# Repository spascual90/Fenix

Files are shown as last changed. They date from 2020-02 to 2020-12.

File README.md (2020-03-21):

# Fenix Autopilot
Fenix Autopilot is an open-source DIY tiller pilot for small boats based on Arduino.

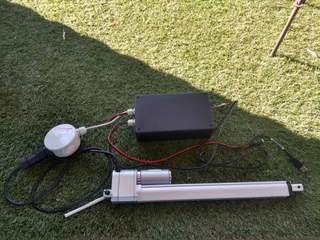
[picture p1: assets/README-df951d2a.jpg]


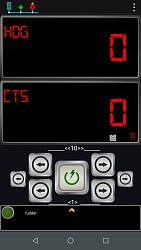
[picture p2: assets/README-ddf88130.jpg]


## Released versions
- V0.1 Initial version

## User Guide
https://spascual90.gitbook.io/fenix-autopilot/

## How to contribute?
Fenix Autopilot is an Open-source project. Source code can be found in Github,
https://github.com/spascual90/Fenix

Fenix Autopilot is developed in the frame of Fenix Project.
The goals of Fenix project are,
- to develop and test a prototype of open-source DIY navigation system for mini-cruisers.  
- to gather individual efforts to a joint solution.
- get users to adopt the system into their own boats with minimum technical knowledge.
All information in Fenix Project can be found here,
https://emacua.fandom.com/wiki/EMacua_Wiki

## How to start with Fenix Autopilot?
First of all integrate your hardware.
If you are a user, upload the SW to Arduino, the App to mobile and configure your autopilot.

If you are a developer, additionally you will have to setup a development environment.
## HW integration
You can find in SCHEMATICS folder,
- Build of materials: the basic shop list to build Fenix autopilot
- Fritzing file
- Guide on how to integrate the components
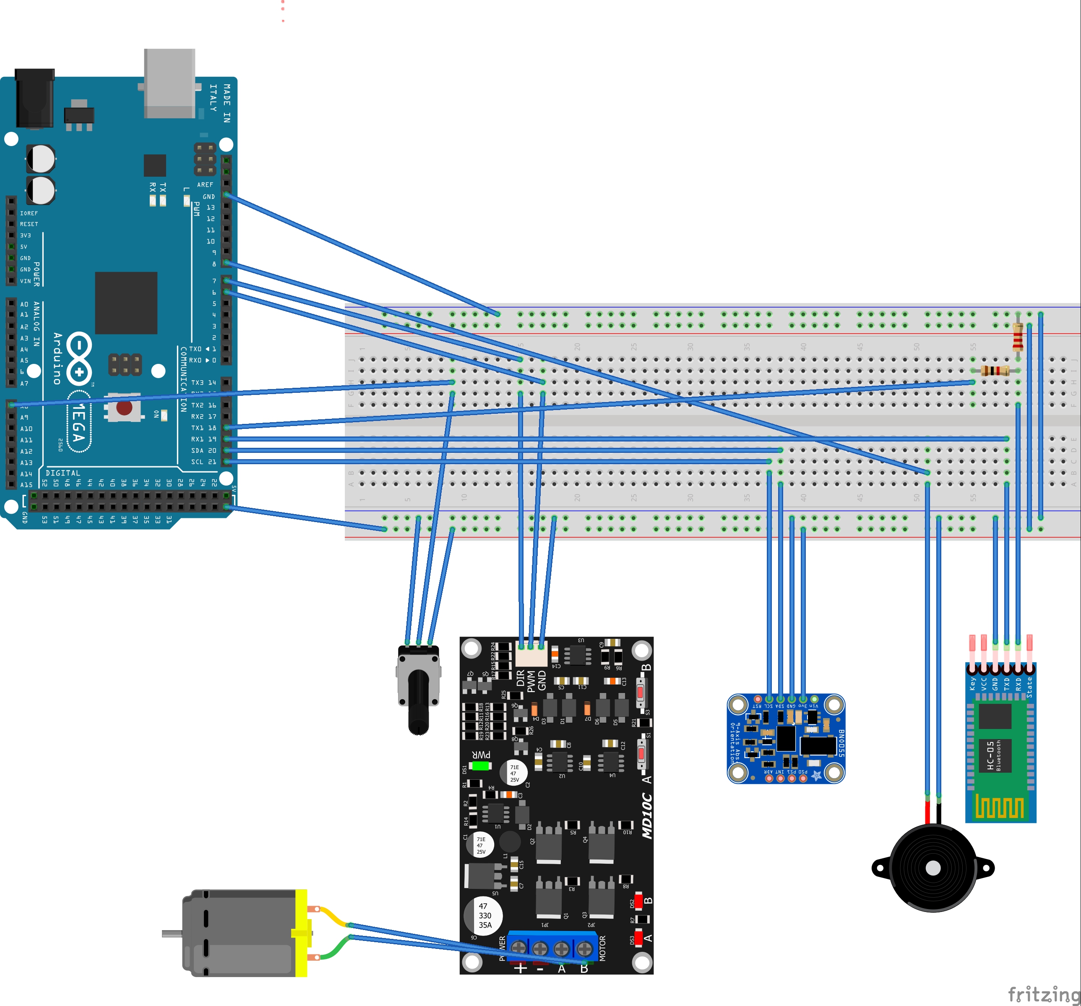
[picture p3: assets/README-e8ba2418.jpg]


## Users: How to start?
### Uploading SW to Arduino
You can find in HEX folder,
- HEX Arduino file
- Xloader, an application to upload HEX to Arduino

### Installing Virtuino App
You can find in repository Virtuino-for-Fenix all elements required
- Enter into Play Store and install Virtuino Viewer
- Copy project file to the Virtuino folder in your mobile
- Configure Bluetooth

### Autopilot configuration
- Connect your laptop to Fenix autopilot USB.
- Open Arduino IDE or putty.exe available in Serial IF folder
- In putty select the Arduino settings
- Open a new terminal
- Follow autopilot information to configure your IMU and linear actuator
- All implemented messages are described in Serial IF folder. A checksum calculator is included.
- Configure other parameters of the autopilot

## Developers: How to start?
### Installation of development environment
Install Sloeber, the Eclipse Arduino IDE https://eclipse.baeyens.it

Downlad Fenix Project from Github https://github.com/spascual90/Fenix

Compile and upload sketch to Arduino

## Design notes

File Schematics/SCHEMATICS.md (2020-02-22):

# Schematics
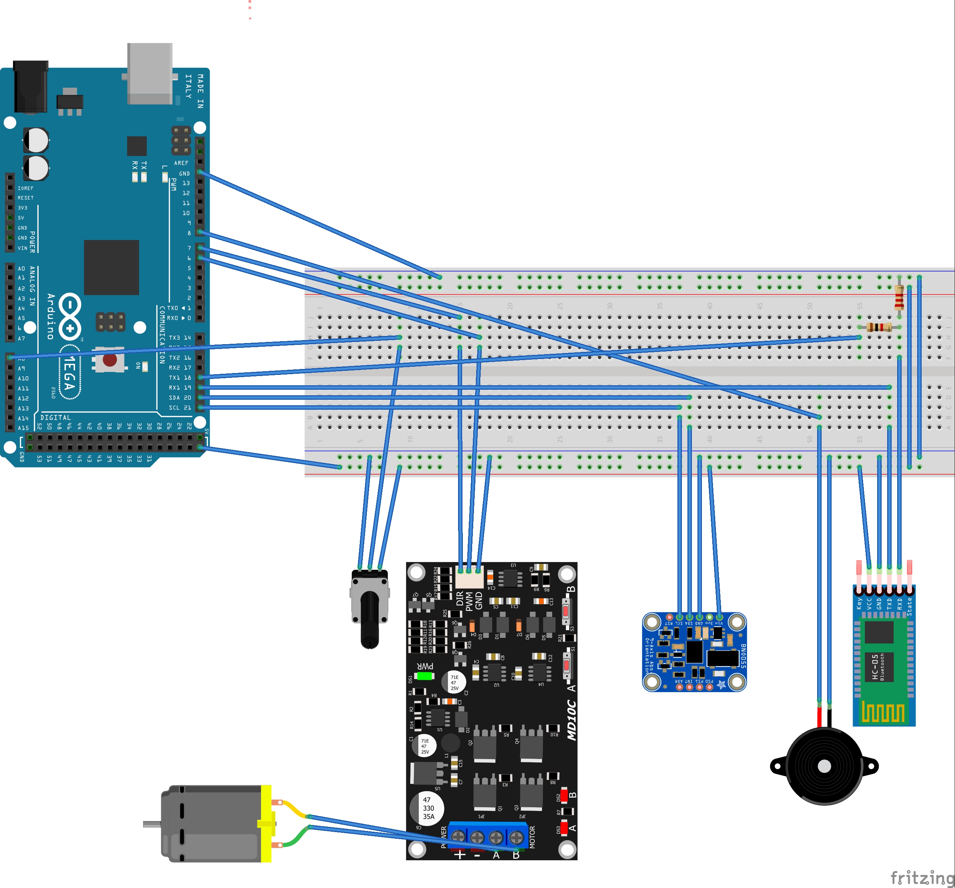
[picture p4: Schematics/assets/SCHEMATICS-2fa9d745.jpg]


## Notes on Schematics & Bill of Materials
- Linear actuator with potenciometer is represented by,
  - M2 - DC Motor
  - R2	Rotary Potentiometer (Small)

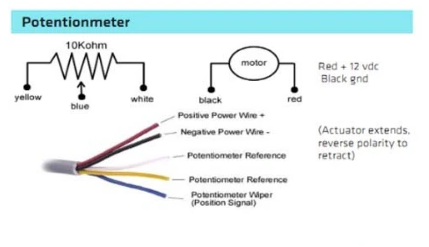
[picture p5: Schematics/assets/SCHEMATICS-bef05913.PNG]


- Alternative DC Motor Driver tested:
  - Cytron MD10C 10A 1 DC motor Driver
  - Cytron 10A 1 DC Motor Driver Arduino Shield

- DC motor driver is powered by a 12V battery not represented.
- Arduino can be powered by 12V battery using a step-down converter to at least 8.5V. Less tension will switch power source to USB leading Arduino to reset if current is too low (USB Laptop OK, Raspberry Pi USB NOK).
- Breaker at the 12V entry should be used for security.

## Notes on IMU BNO055
- I2C shall be connected to GND
- Shortcircuit S0 and S1 negative poles
- Install oscilator into available places

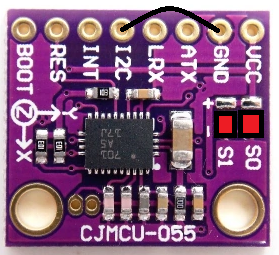
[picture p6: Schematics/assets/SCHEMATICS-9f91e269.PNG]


## Notes on HC-05 BT
- BT shall be configured to 38400 Bauds. Use BT_AT_Mode sketch

# Prototype assembly






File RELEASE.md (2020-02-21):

# RELEASE
## Version: 0.1
## System requirements
| Req.ID# | Description | Criticity | Implemented |
| --- | --- | --- | --- |
| SR-1 | Minimize cost of adquisition. Based on COTS components and integrate Open-source projects as possible | High | Yes |
| SR-2 | Ease integration with other systems or components by using industry standards. | High | Yes |
| SR-3 | Ease system adoption from developers and users with appropriate documentation, minimizing requirements for technical knowledge on electronics, physics or SW. | High | No |
| SR-4 | Modular approach priorizing escalability of components to implement requirements in later stages. Use of object oriented code. | High | Yes |
| SR-5 | Provide test means in order to ease testing and recording of results | High | Partial |

## Autopilot requirements implemented
| Req.ID# | Status | Description | Priority |
| --- | --- | --- | --- |
| AP-3 | Closed | Minimize power consumption | High |
| AP-4 | Closed | Internal compass tilt compensated | High |
| AP-6 | Closed | Calibration procedure for internal compass before installation supported by Autopilot without additional OEM SW. | High |
| AP-7 | Closed | Compensation of permanent deviation of installed compass with reference to the bow. | High |
| AP-18 | Closed | USB electrical interface. | High |
| AP-19 | Closed | Alternative NMEA 0183 version 2.x or | High | er electrical interface (RS422). | Nice to have
| AP-20 | Closed | NMEA 0183 data protocol at least versions 2.x to 4.x (4800 baud, w/o parity, 8 bits,1 bit stop) | High
| AP-22 | Closed | Reception of minimum autopilot information required for Nav mode | High
| AP-24 | Closed | Transmision of internal compass magnetic course. | High
| AP-25 | Closed | Transmision of tiller position. | Low
| AP-27 | Closed | Stand-by mode provides user capability to command linear actuator changes in and out by short and long leaps. | High
| AP-28 | Closed | Compass mode. Autopilot will follow the current course. | High
| AP-31 | Closed | Nav mode. AP will bear to a Waypoint by following the required course received from an external source. | High
| AP-34 | Closed | User definable central position of tiller | High
| AP-35 | Closed | Adjust AP bearing during Autopilot mode by 1º or 10º | High
| AP-39 | Closed | Ensure safety of the operations by requiring user confirmation before proceed and/or sound warning (i.e. error, start, stop, tack, decission/ action of user required...). | High
| AP-40 | Closed | Minimum recomended motor controller performance: Bidirectional single-brushed. Support motor voltage to 16V. Support continous current: 10 A | High
| AP-41 | Closed | Voltage threshold: 10-16V | High

# Autopilot requirements not implemented

| Req.ID# | Status | Description | Priority |
| --- | --- | --- | --- |
| AP-2 | Closed | Protection by design of mechanical and electronic parts from blockage, intense use, short-cirtuit and humidity. Parts exposed to weather conditions shall have IPX4 equivalent protection. | High |
| AP-5 | Closed | Capability to use as alternative an external compass  | Nice to have |  
| AP-9 | Closed | Mounting at starboard or portboard | High |
| AP-10 | Open | Autotrim of tiller to keep current heading when lateral forces (wind, tide, non-centered engine) require permanent correction of tiller to follow the current way-route. Maximum 1 minute for autotrimming. | To be cheked | | | | |
| AP-11 | Closed | Predefined pilot gain configurations for different speeds and boats. | High  |
| AP-12 | Closed | Autogain for different SOW (speed over water).  | Low |
| AP-13 | Closed | If SOW is not available, user configurable speed shall be used. | AP.-14  | Closed | User configurable gain for testing purposes. | High |
| AP-15 | Closed | Capability to record required parameters to analyze AP performance for different external conditions for testing purposes. | High |
| AP-16 | Closed | Different deadband configurations for bad weather conditions: predefined, user defined, desactivated. | High |
AP-17 | Closed | Automatic deadband configuration  | Nice to have |  
 AP-21 | Closed | Reception of magnetic/real course from external compass | Nice to have |
AP-23 | Closed | Reception of SOW information from nautical slide. In Km or nautical miles. | Low |
  | AP-26 | Closed | Reception of real and apparent wind information. | High |
  | AP-29 | Closed | Wing mode. AP will maintain current Apparent Wind Angle. | Medium |
  | AP-30 | Closed | Wind mode is only possible when wind information is available from an external source. | Medium |
  | AP-32 | Closed | Nav mode. If not available from external source, the required course will be BTW. | Nice to have |
  | AP-33 | Open | Central position of tiller is by default considered the position where Autopilot is set to Compass mode. | Low |
  | AP-36 | Closed | Tack starboard/ portboard in Compass mode. AP will turn by 100º the current heading in the direction selected by the user. | High
| AP-37 | Closed | Tack in Wind mode. AP will turn to head the same Real Wind Angle but on the oposite band. Turn direction will be selected by AP as the shortest path to reach the target heading. | High |
 | AP-38 | Closed | Tack in Nav mode is not possible. | High |
  | AP-42 | Open | Maximum thrust torque (at the end of the tiller): 250N. Minimum angular speed (tiller): 0 Kg: TBD º/sec 35 mm/seg 20 Kg: TBD º/sec 30 mm/seg 40 Kg: TBD º/sec 20 mm/seg | High |

## Requirements partially implemented
| Req.ID# | Status | Description | Priority |
| --- | --- | --- | --- |
| AP-8  | Closed | Procedure to define installation parameters supported by Autopilot without additional SW. | High |

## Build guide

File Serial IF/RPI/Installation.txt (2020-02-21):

Install and Run Putty on your Raspberry Pi
Putty is a very useful application that can be used to connect to serial ports and Secure Shell(SSH) to Raspberry Pi’s.

Putty is mostly used on Windows to connect to remote devices but it can also run on a Raspberry Pi.

Steps to installing Putty on a Raspberry Pi:

Open a terminal/shell window on your Raspbery Pi and run the following command:
sudo apt-get install putty -y
After the installation Putty should appear in the menu bar under the ‘Other’ menu.

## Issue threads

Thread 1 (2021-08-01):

conflict between libraries (multiple definitions)

elgui, 2021-08-01:
I'm using the provided versions of external librairies, and the build fails due to "multiple definition" of many sorts.
I have read that it comes from conflicting librairies, using the same interupt pin or timer.

```
Disabling relaxation: it will not work with multiple definitions
make: *** [makefile:93: Fenix.elf] Error 1
multiple definition of `__vector_25'
multiple definition of `__vector_26'
multiple definition of `__vector_36'
multiple definition of `__vector_37'
multiple definition of `__vector_51'
multiple definition of `__vector_52'
multiple definition of `__vector_54'
multiple definition of `__vector_55'
multiple definition of `NeoHWSerial::available()'
multiple definition of `NeoHWSerial::begin(unsigned long, unsigned char)'
multiple definition of `NeoHWSerial::end()'
multiple definition of `NeoHWSerial::flush()'
multiple definition of `NeoHWSerial::peek()'
multiple definition of `NeoHWSerial::read()'
multiple definition of `NeoHWSerial::write(unsigned char)'
multiple definition of `NeoSerial'
multiple definition of `NeoSerial1'
multiple definition of `NeoSerial2'
multiple definition of `NeoSerial3'
```

spascual90, 2021-08-01:
Hello, difficult to analyze as I am on holidays, no access to my test platform... sorry.
I think this is related to wrong configuration of the library path folders.
Are you using Eclipse or the Arsuino IDE?
If you give more info related to this topic I may help for troubleshooting.

Regards
Sergio

elgui, 2021-08-03:
Hello Sergio,
thank you for answering while being in vacations !
Following your  hint, I found the problem : I had duplicate NeoHWSerial files...
I have struggled so much to setup that workspace that it endep-up a bit messy.. But now it works, and as a developer, I'm super happy to further participate in that project !
I keep you posted, enjoy your holidays =)
PS: I am anchored in the South-West of Andalucia (just in case)

Closed 2021-08-03.

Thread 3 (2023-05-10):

BOM

tcurdt, 2023-05-10:
Quick correction of the docs:
A BOM is a "Bill of Material".

Very cool project!

spascual90, 2025-01-05:
Thank you and apollogize for the very late answer. Will check the documentation and fix.
Regards
Sergio

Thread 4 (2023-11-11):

JP2-Kypad

Max194703, 2023-11-11:
Hi, is it possible to add a keypad?

spascual90, 2025-01-05:
Hello,
the short answer is currently no, but can be developed.
I started developing Fenix using a keypad and evolved to a bluetooth connection to the mobile, which provides robust connection and better graphic interface. Keypad code was discontinued and nowadays not supported.
Alternative: I recently checked USB connection from Fenix to a mobile using an OTG cable and Serial USB Terminal. If you want a wired connection, this is a good alternative using NMEA messages for basic functions (RUN/STAND BY, TURN STARBOARD/ PORTBOARD). I will further develop this idea soon in a video.

Regards
Sergio

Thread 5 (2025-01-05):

Use with PyPilot motor controller

mgrouch, 2025-01-05:
I have Pypilot motor controller for hardware. And bunch of esp32 from m5stack. I’d like to see if I can use fénix autopilot MCU to control motor controller from Pypilot.
I didn’t do much of homework on this yet but I’d appreciate any leads.

Thanks

spascual90, 2025-01-05:
Hello,
Fenix has a standard PWM based control interface. If Pypilot uses this standard it will be easy to integrate.

I had a look to the documentation available for the Pypilot motor controller but it requires time to understand... I think Pypilot is a project much more complex than Fenix with a lot of implementation alternatives and configurations.

It would be interesting to other users moving from Pypilot to Fenix to know if they can reuse part of their hardware. Any progress on this will be welcome!

Regards
Sergio

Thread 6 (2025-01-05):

Ordering PCB

mgrouch, 2025-01-05:
Is there a way to ask https://jlcpcb.com/
(as it seems it’s most common)
instead of uploading the schematics again
just to provide some reference number of previous order and repeat it? I think it would simplify the process for manufacturer and end user as well.

Thanks

spascual90, 2025-01-05:
Hello,
I am not aware of it. If you find it, let me know what is the required code and I will check in my last order if I can provide it to you.
However, if you need help to order on jlcpcb.com let me know and I will be glad to support.
Regards
Sergio

Tempest2k8, 2025-01-22:
@mgrouch I have extra boards, as the minimum order was 5. I've ordered the other parts for the shield from Aliexpress and can package them in a kit if you would like one.

Chris

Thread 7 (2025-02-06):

IMU Out of range / ICM20948

PlavB, 2025-02-06:
Hello,

I am having issue calibrating the IMU Sensor from Sparkfun. Using the python software as shown in the recent youtube video.

After calibrating i get the error message "IMU offsets out of range" after it uploades the NMEA Sentence for each of the offsets(Gyro, Acc and mag)

Testing the accuracy after uploading the data to arduino it is working ok with some deviation, but after a reboot it will be way off with the heading accuracy. Often being stuck between a certain posistion range (e.g: 120 - 190).

I have tried to calibrate it a few times at different locations, could this be an issue? And is it possible to remove previous data/calibration attempts?

spascual90, 2025-02-07:
Hello.
Please send me all files generated by python calibrator and will check.

Thank you
Sergio

El vie, 7 feb 2025, 1:25, PlavB ***@***.***> escribió:

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

PlavB, 2025-02-07:
Hello,

See attached file. Thanks.

[Fenix_ICM_20948_Cal-Out of range.zip](https://github.com/user-attachments/files/18704404/Fenix_ICM_20948_Cal-Out.of.range.zip)

spascual90, 2025-02-07:
Hello,
after reviewing your files everything is correct. I used those with my Arduino and it loaded all three NMEA sentences without error message.
You can see attached the output file from the serial comunication with Arduino.

This is the info I got from your files,

*************************
******* GYROSCOPE *******
*************************
G_offset[3] = { -83.13,-118.02,31.29 };

*************************
NMEA Sentence for Fenix Autopilot :
*************************
$PEMC,14,-83.13,-118.02,31.29,0.00000,0.00000,0.00000,0.00000,0.00000,0.00000,0.00000,0.00000,0.00000,G*63

*************************
***** ACCELEROMETER *****
A_B[3] = {-3.39,-255.08,365.69 };

A_Ainv[3][3] = {
{ 0.06021 , 0.0027 , 0.00081 },
{ 0.0027 , 0.06175 , -0.00059 },
{ 0.00081 , -0.00059 , 0.05993 }};
*************************
NMEA Sentence for Fenix Autopilot :
*************************
$PEMC,14,-3.39,-255.08,365.69,0.06021,0.00270,0.00081,0.00270,0.06175,-0.00059,0.00081,-0.00059,0.05993,A*65

*************************
***** MAGNETOMETER *****
*************************
M_B[3] = {124.03,295.09,30.58 };

M_Ainv[3][3] = {
{ 3.11726 , 0.08012 , 0.23037 },
{ 0.08012 , 3.4981 , -0.00322 },
{ 0.23037 , -0.00322 , 2.82628 }};

*************************
NMEA Sentence for Fenix Autopilot :
*************************
$PEMC,14,124.03,295.09,30.58,3.11726,0.08012,0.23037,0.08012,3.49810,-0.00322,0.23037,-0.00322,2.82628,M*5D

According to Arduino code, the error message shall pop up when any of the values exceed the following limits,
G_offset[3] +-1000
A_B[3] +-1000
M_B[3] +-1000
A_Ainv[3][3] +-50
M_Ainv[3][3] +-50

And the NMEA sentences you generated are within the limits. There should not be any error.

Can you copy the serial output with Arduino so I can see the error message in context?
To do so, just select all lines and copy (press Ctrl+C) then paste to a .txt file.

Thanks
Sergio

[Serial_output.txt](https://github.com/user-attachments/files/18710308/Serial_output.txt)

PlavB, 2025-02-07:
Hello,

I can see that it failed to load the install parameters, for your information, i have not changed any settings.

[Copy of serial output.txt](https://github.com/user-attachments/files/18710531/Copy.of.serial.output.txt)

spascual90, 2025-02-07:
Please repeat the process to send 3 nmea sentences and send the serial so I can see the error.
Thank you

Regards
Sergio

PlavB, 2025-02-07:
Hello,

This should be it:

[Serial output nmea.txt](https://github.com/user-attachments/files/18711250/Serial.output.nmea.txt)

spascual90, 2025-02-07:
Try to load in a different order. First M then G and finally A.
Regards
Sergio

El vie, 7 feb 2025, 23:54, PlavB ***@***.***> escribió:

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

PlavB, 2025-02-07:
Same issue, unfortunatly.

Sensor is working ok after sending the offset data, but as soon as it is being rebooted it gets the same error .

PlavB, 2025-02-07:
Hello again,

I might have found the issue. I cleared the EEPROM using the example code "EEPROM_Clear" in the arduino IDE software.

Reinstalled the HEX File and the calibrator data. Now after several reboot it keeps the same offsets and no alarm.

There were probably too many different configurations stored in the EEPROM. During the installation process i also tested with the BNO055 IMU.

Just one question regarding the Serial interface. I am not able to send commands through either Arduino IDE or Putty. It does not respond, is there an easier way to send the commands?

Thank you for your help so far. :-)

spascual90, 2025-02-08:
Good to hear that. I will think about an instruction to reset the eeprom.
For serial communication with Arduino ide, once  Board and Port are selected, you should configure the monitor at 9600 Baud and "No line ending" option.
It works for me.
Regards
Sergio

PlavB, 2025-02-10:
Hello,

I think I was a little quick to confirm that everything was working 100%. Sorry about that.

It seems that when I try to change the settings in the Installation Parameters/PID Parameters, the IMU offset is again going out of range.

I can set up the IMU with the calculated offsets just fine, but when I try to change the parameters, save, and then reboot, the offsets are gone from the Arduino. If I try to do it in reverse; changing the parameters first and then uploading the offsets, the parameters are gone, but the IMU offsets remain.

I can also mention that i am not able to save the Installation Parameters at first with a fresh HEX installation.(Prompted with Failed to restore inst.parameters, loading default")

I have to install the "Simulator" HEX file to save the installation parameters once, then go back to the ICM HEX file, after that i am fully able to change and save the installation parameters. But it seems i am not able to save both installation/PID parameters and the IMU offsets. Could there be anything wrong with my Arduino? It is a fresh unit.

Regards,

Olav H.

spascual90, 2025-02-10:
Thank you to your comments I identified a bug in the code.
Please check new pre-release and give feedback. It should fix the issues you are facing. All IMU, Inst.Parameters are related to overwritting directions in EEPROM.

https://github.com/spascual90/Fenix/releases/tag/v3.4beta2

Regards
Sergio

PlavB, 2025-02-10:
Hello,

I have now tested it, and it has resolved the issue. Tried to change the settings on both installation and pid parameters after setting up the IMU offsets and it worked wonders. Thank you.

I will do a another sea trial tomorrow. 👍

Regards,

Olav H.

spascual90, 2025-02-11:
Good to hear that!
Please make video and picture of your installatuon and share experience!
Regards
Sergio

El lun, 10 feb 2025, 22:54, PlavB ***@***.***> escribió:

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

Closed 2025-02-11.

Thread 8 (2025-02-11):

Installation parameters / Sea trial questions

PlavB, 2025-02-11:
Hello,

Some question/findings during sea trial(Sorry for the repetetive questions, i am not so familiar with fault finding in code),

I am not able to change the average cruise speed in the installation parameters.(System in standby-mode).

I noticed that when choosing a CTS/HDG, example: 120. At standstill the rudder is fixed to the correct heading, but as soon as i accelerate the boat it turns 180 degree and follows that heading, so if i choose 120, when boat start to move, it will follow the HDG of 300 degrees.

Can this be because i can't change the average cruise speed? Or is this about the heading allignment? My boat is capable of moving about 15-16knots maximum. But cruising is more like 5-10 knots.

Just to clarify, Is the Centered tiller posistion setting supposed to be the potentiometer value when tiller is alligned with the hull? For example mine is showing 338 in the actuator calibration menu in the application, should this value be the setting in the installation parameters? Or is it always 0?

Note; I also noticed that i can not change the mounting posistion of the actuator. Not a real problem for me, since mine is mouinted on Starboard side.

Thank you very much for your support.

Olav H.

PlavB, 2025-02-11:
Additional note,

I am not able to change the rudder angle parameter. it is locked to default 511.

spascual90, 2025-02-12:
Hello,
Average Cruise is currently not used by the autopilot. Is there for future improvements.

To start to work you just have to go through calibration of linear actuator.
To check good calibration, on stand by press > button until the actuator is fully extended and then press < until it is fully retracted. Finally press Start and it should go to the center position.

For more information about the 180 turn I would need the serial dump again and/or some videos.

Regards
Sergio

spascual90, 2025-02-12:
> Additional note,
>
> I am not able to change the rudder angle parameter. it is locked to default 511.

Do you mean maximum rudder angle?
511 should be the standard value. Change only if you want to limit the extension of linear actuator.
Regards
Sergio

spascual90, 2025-02-13:
And IMU device shall be placed horizontal with the components on top and away from magnets like buzzer or boat engine.
Regards
Sergio

PlavB, 2025-02-13:
Hello, Sorry for delayed answer. Didnt have the oppertunity to go on a boat trip until today.

Thanks for clearifying the questions.

I think the IMU  is placed away far enough from magnets and engine. Engine is 1 meter approx.

Check the link for video of the problem regarding heading being 180 degree out when in motion. I tried the heading allignment without change.

Serial dump:

[Serial dump.txt](https://github.com/user-attachments/files/18787272/Serial.dump.txt)

Link for video and picture of connection box:

https://1drv.ms/f/c/3776124397745f29/Epm12N7_6bxEgwY9ot4zWtEBdGheQyx0pYUHzCZe9nfNkg?e=9gyMWR

spascual90, 2025-02-13:
Hello,
looking at your PID parameters,
$PEMC,05,1.00,0.05,0.00,100,A*74
I think the problem is that the rudder gain (P value of PID) is 1 which is very low. The rudder is not turning enough to steer the boat to the targeted direction.
Try Proportional gain P=8.00 to start.
$PEMC,06,8.00,0.00,0.00,100,m*57

Here a link on how PID works and what is the behaviour of the autopilot depending on the value of P, I, D parameters.
https://www.bandg.com/blog/autopilots-understanding-performance-functions/

You can follow this guide to calibrate your PID values that fit to your boat's behaviour. Start with P, then I and finally D.

Regards
Sergio

PlavB, 2025-02-13:
Hello,

I will check tomorrow. Thanks.

I was experiencieng a lot of sway with 8. I supose i didn't use the I and D correctly.

Will revert with the results!

spascual90, 2025-02-19:
Hello,
Any progress? Tweaking PID parameters to get good results can be difficult. I have no trusted process defined. Whether to start with I then PD or PD then I...
Regards
Sergio

PlavB, 2025-02-19:
Hello,

I havent had so much time to go out and test since it has been snowing a lot.

I tried with only changing the PD but i get too much side to side movements, i find it to work best with P: 1 and D: 0,5 so far.
I will try changin the I first as well.

Maybe the actuator is too slow or the rudder angle is too big? i will try to adjust this on the next test run.

Just to mention, i still have the issue that it is tracking 180⁰ wrong. Even with P being 8.

I have also noticed that i can only change next CTS by turning the heading weel towords starboars and not portside.

PlavB, 2025-06-06:
Hello,

I haven’t had much time to test due to work.
I’m sure I calibrated the actuator correctly, but I’ll definitely double-check it. Thanks for noticing.

Will revert as soon possible. But i dont think i will get the chance untill august, unfortunatly.

Regards, Olav

spascual90, 2025-06-08:
Maybe you did not save after calibration? Please let me know any progress. Also complete log would help to sort out.
Sergio

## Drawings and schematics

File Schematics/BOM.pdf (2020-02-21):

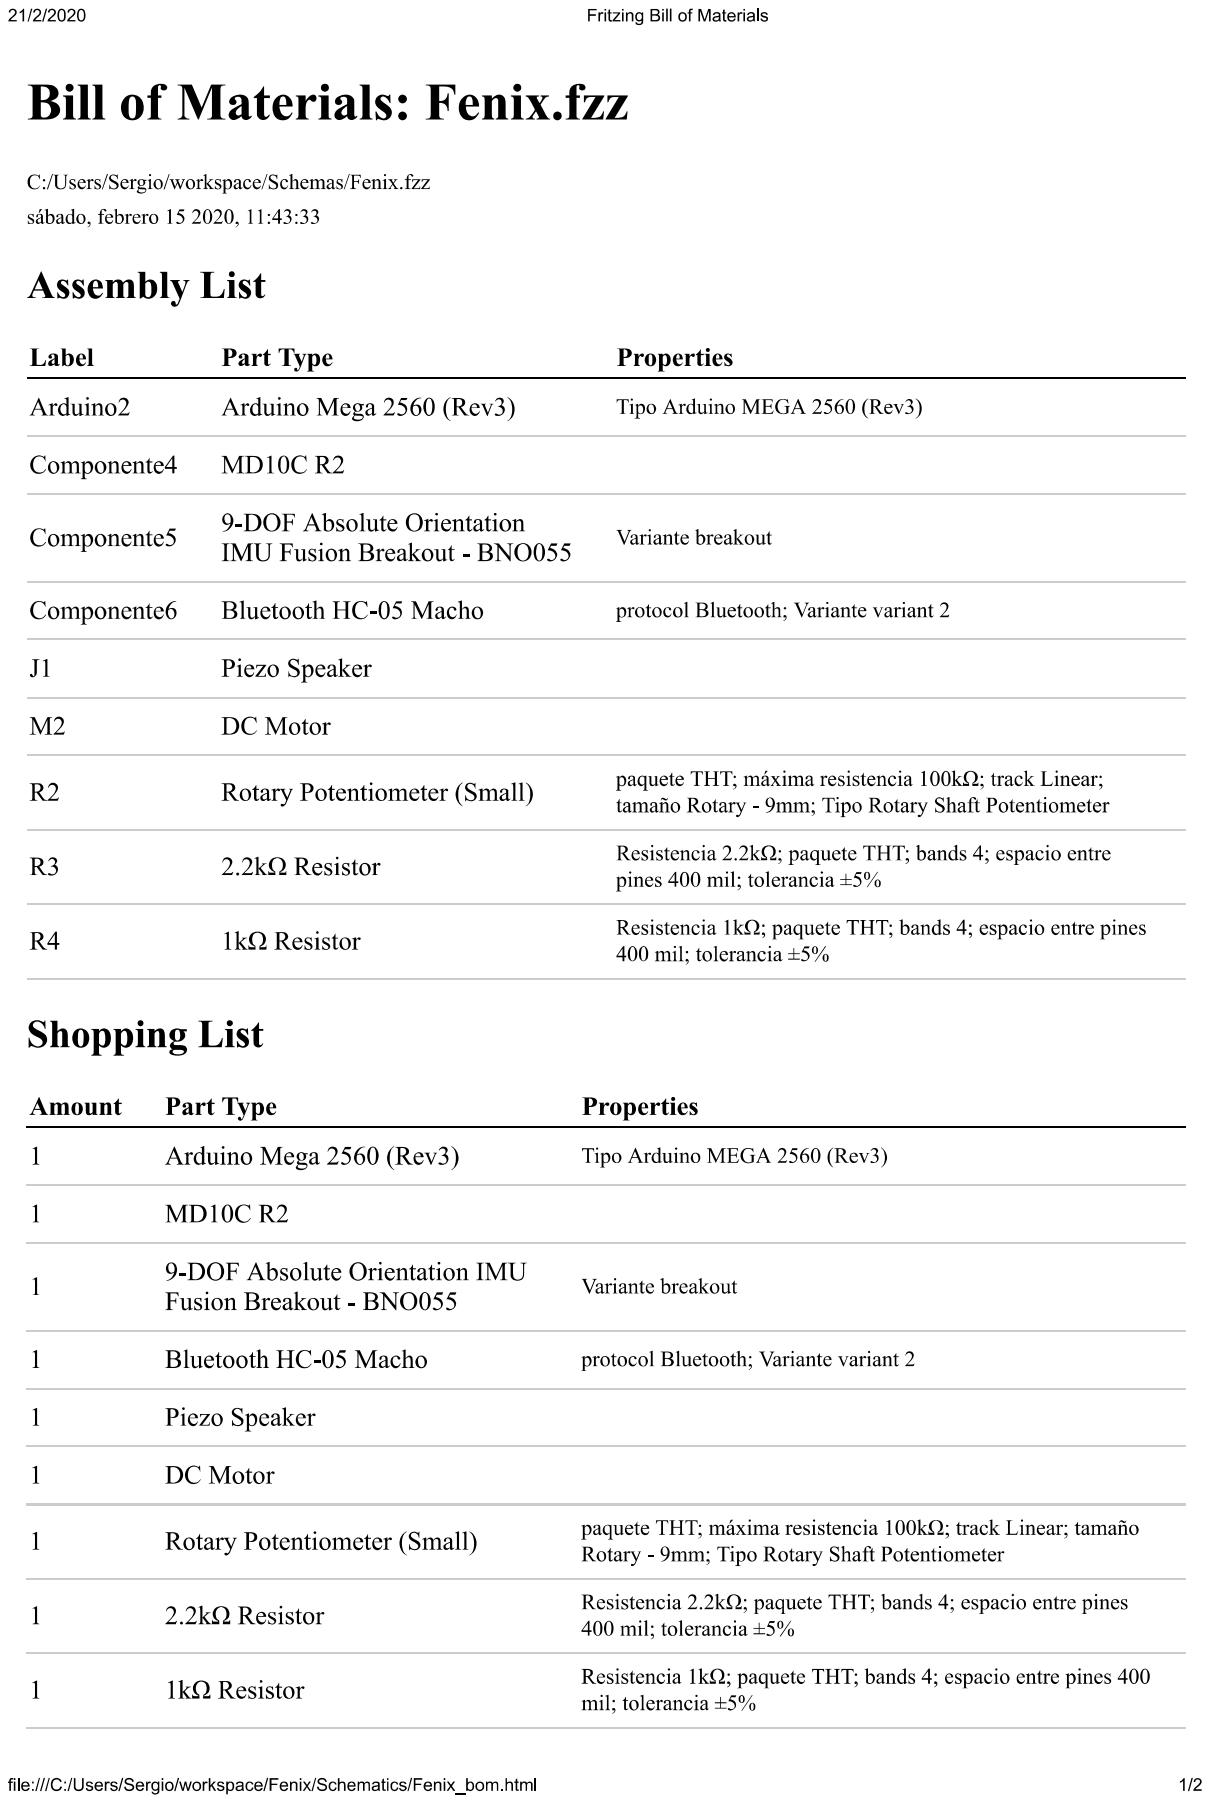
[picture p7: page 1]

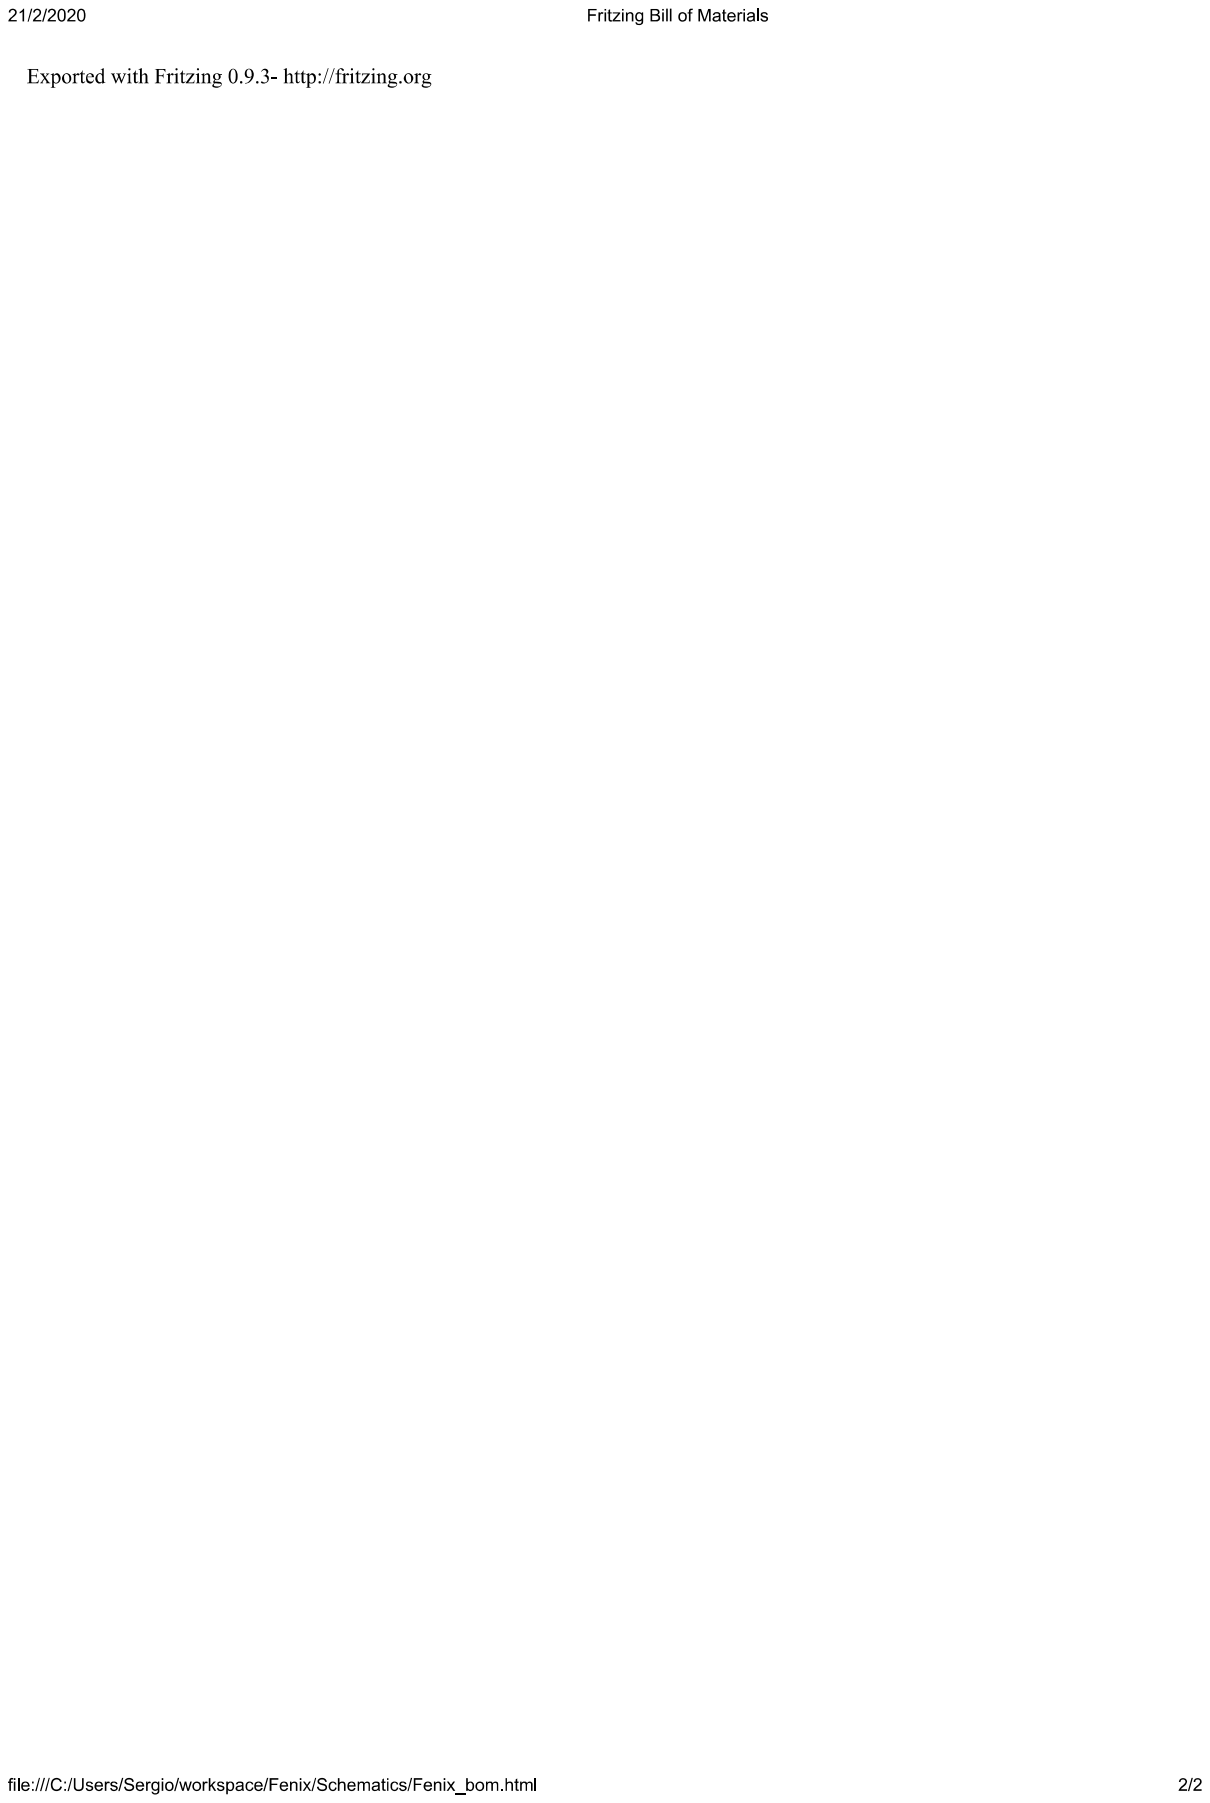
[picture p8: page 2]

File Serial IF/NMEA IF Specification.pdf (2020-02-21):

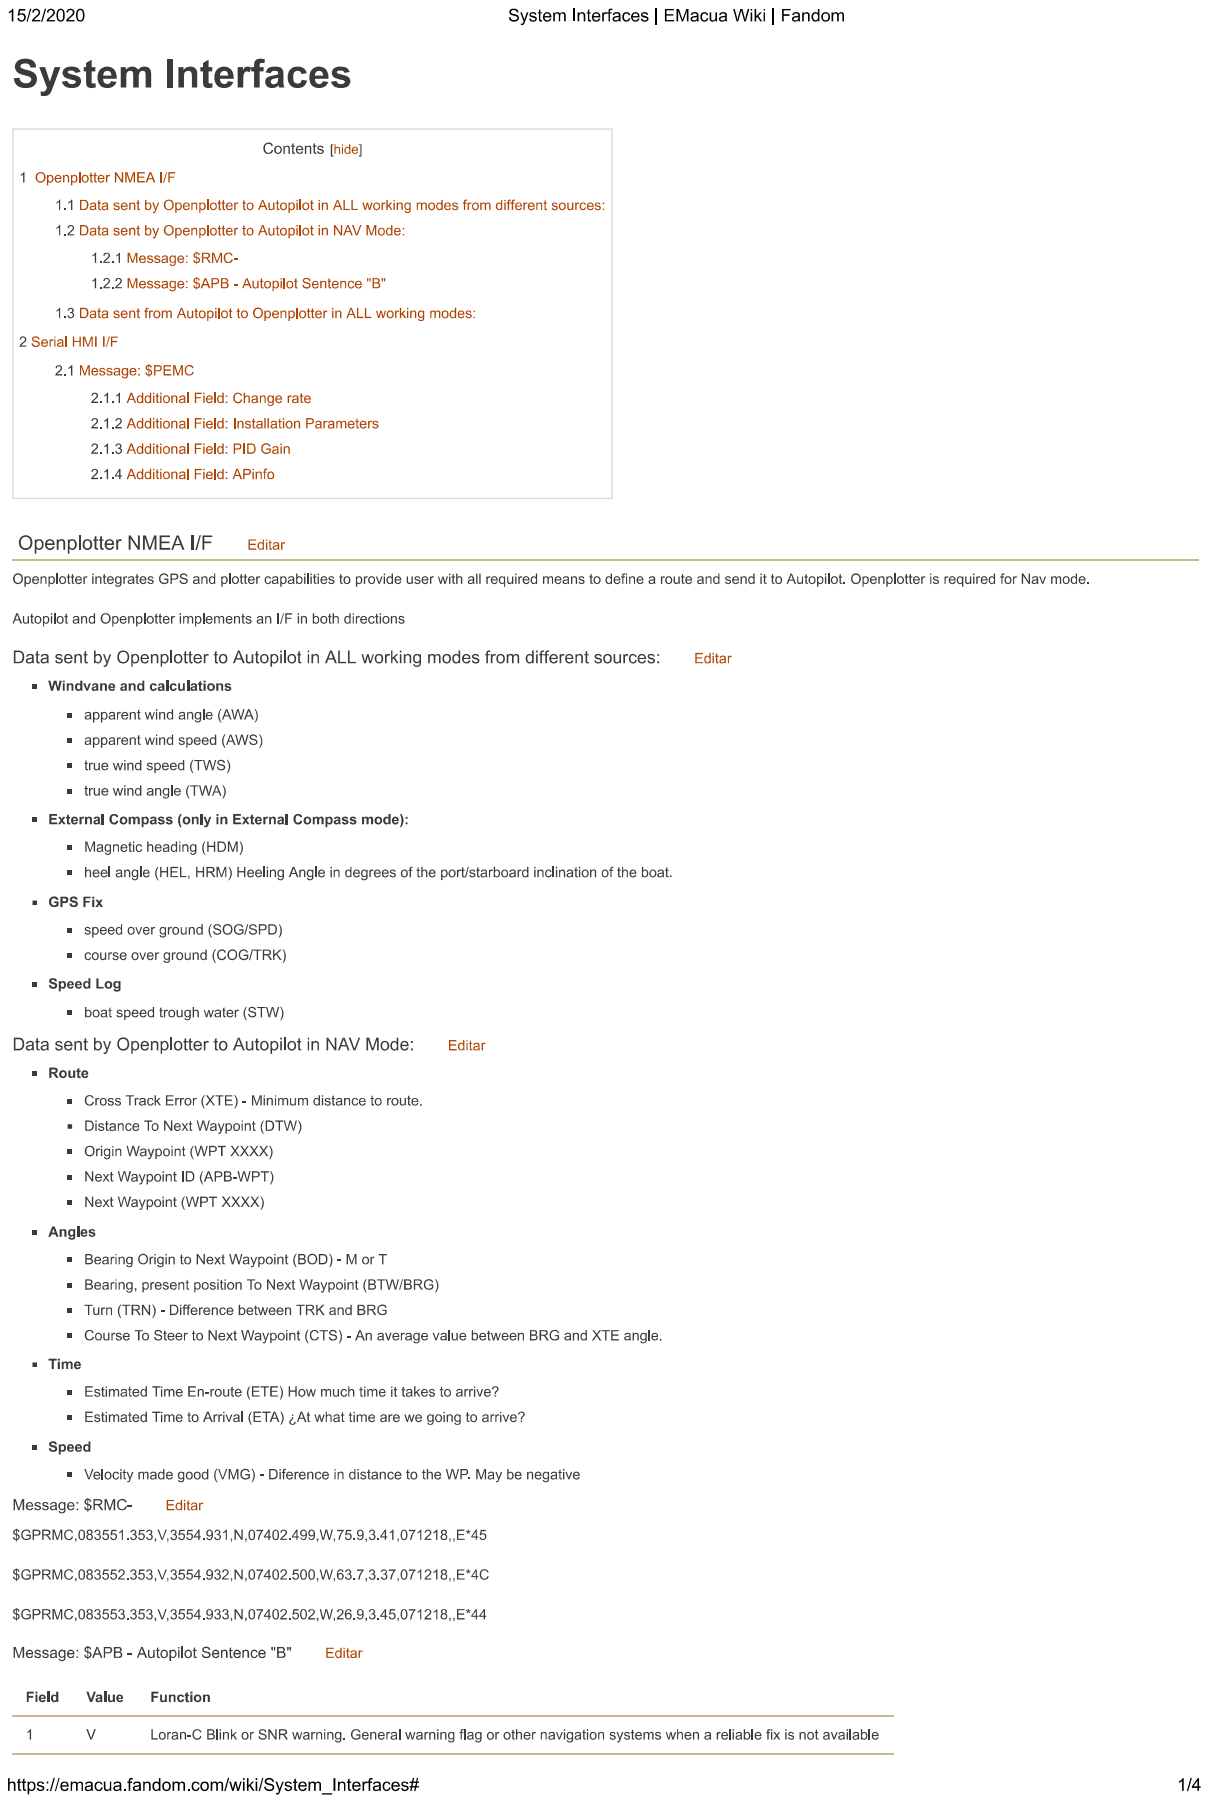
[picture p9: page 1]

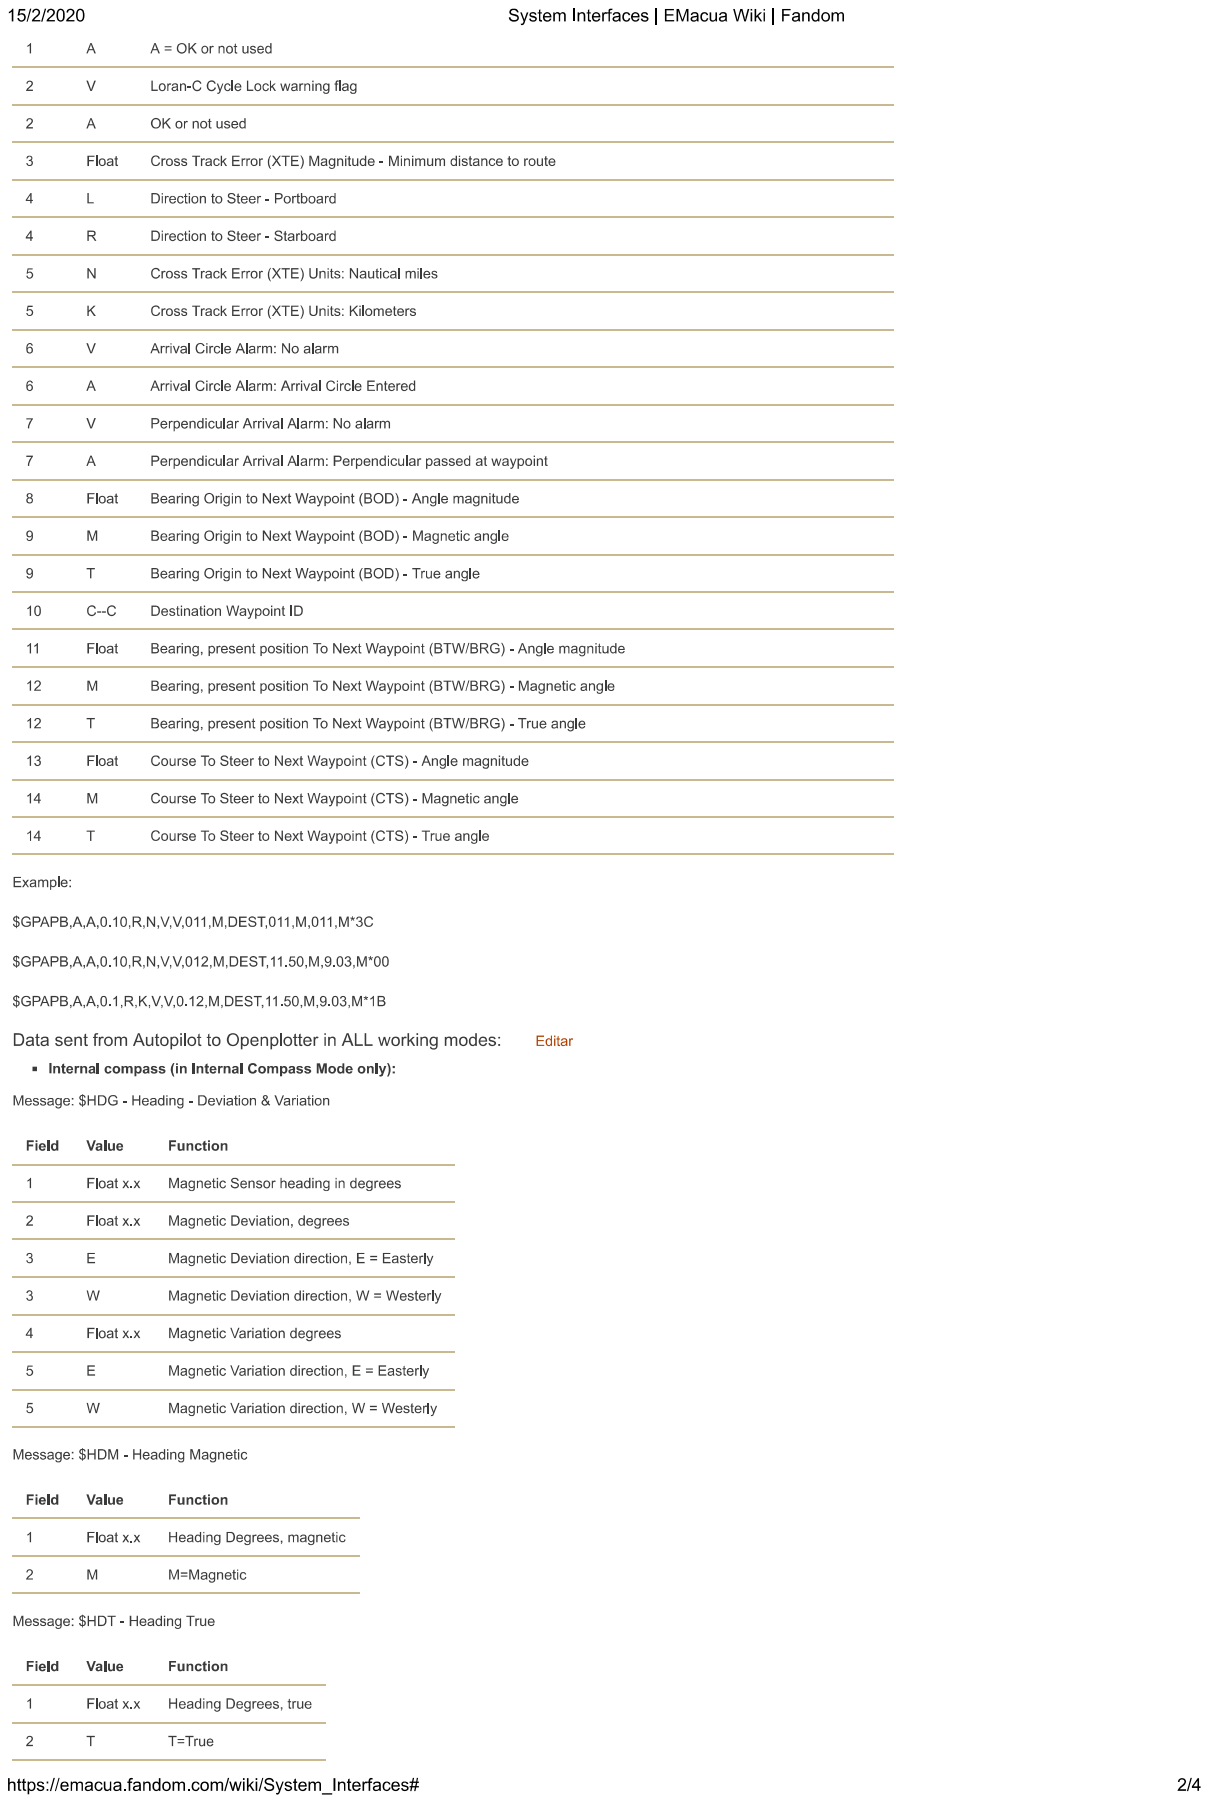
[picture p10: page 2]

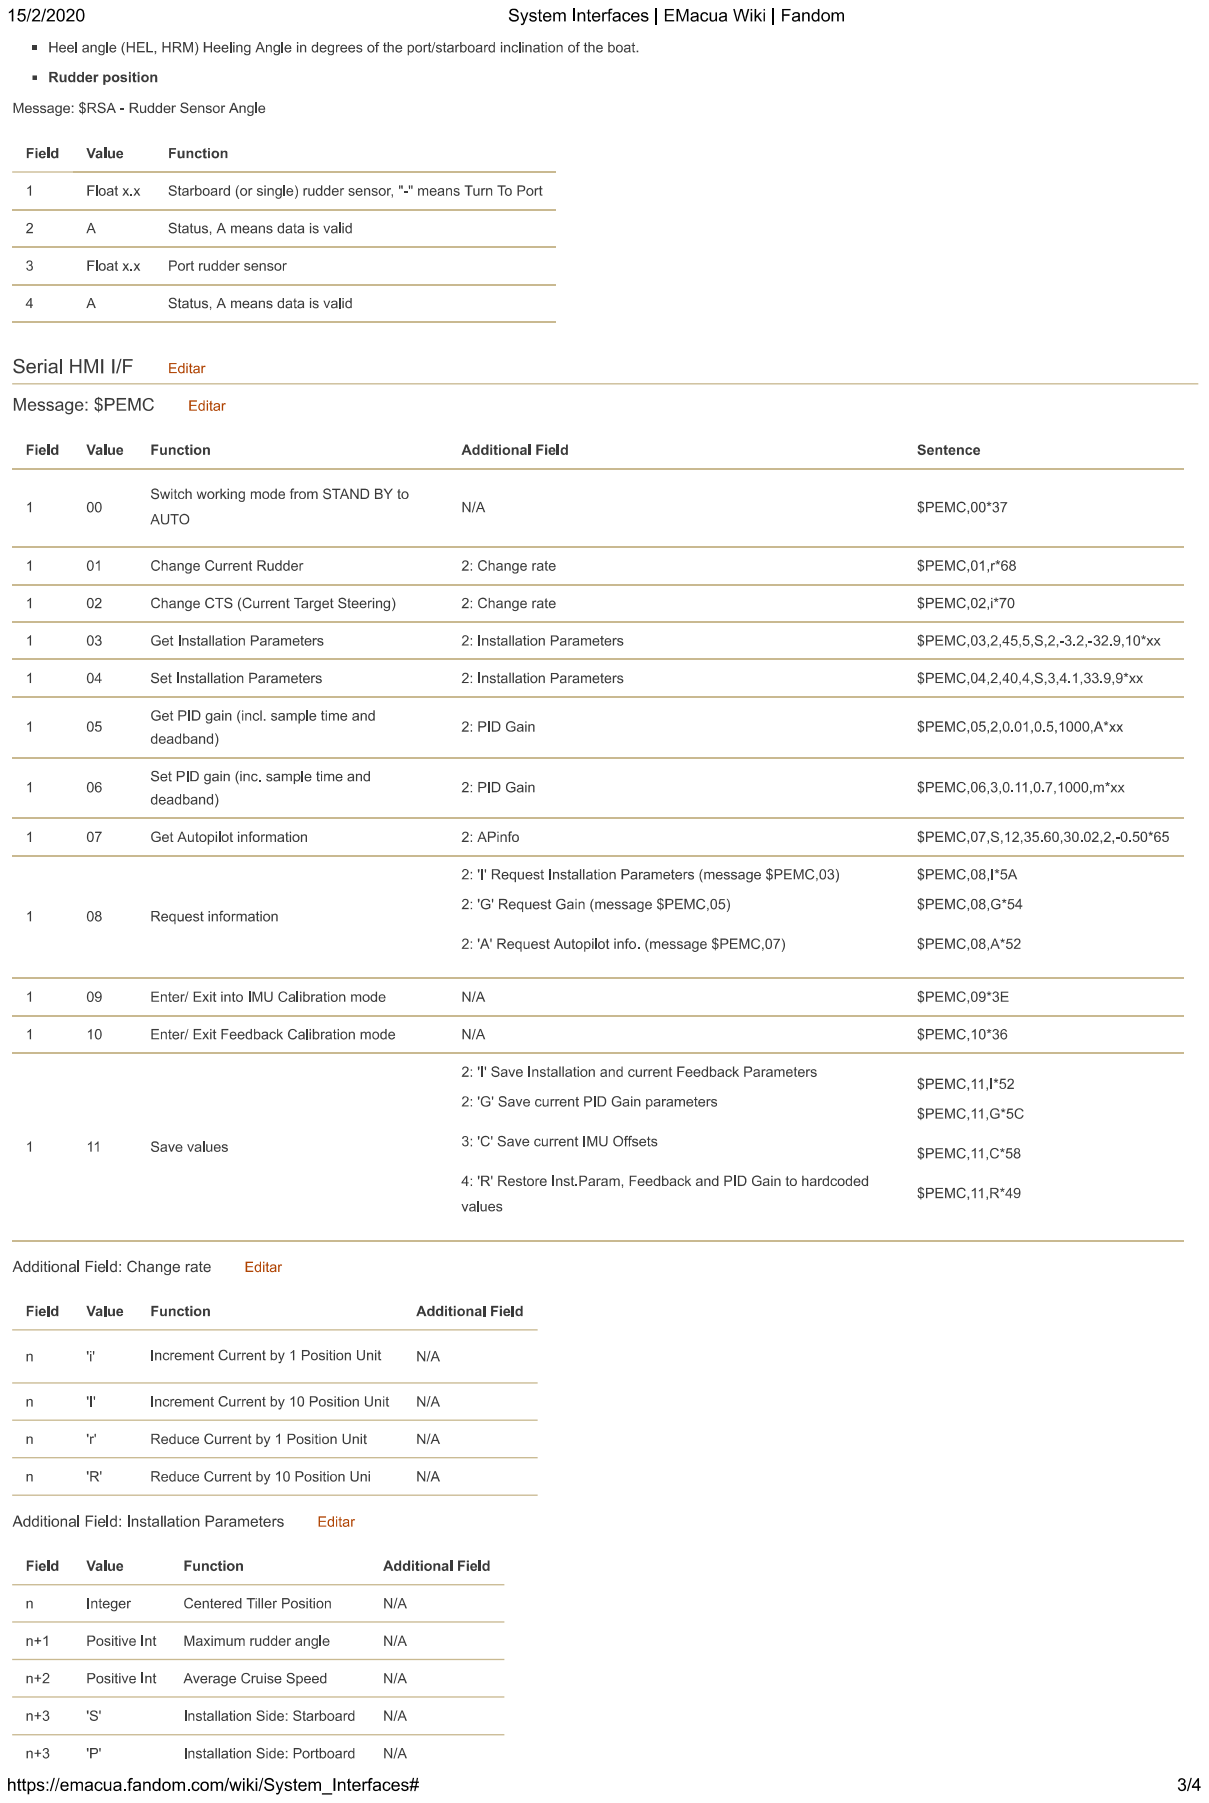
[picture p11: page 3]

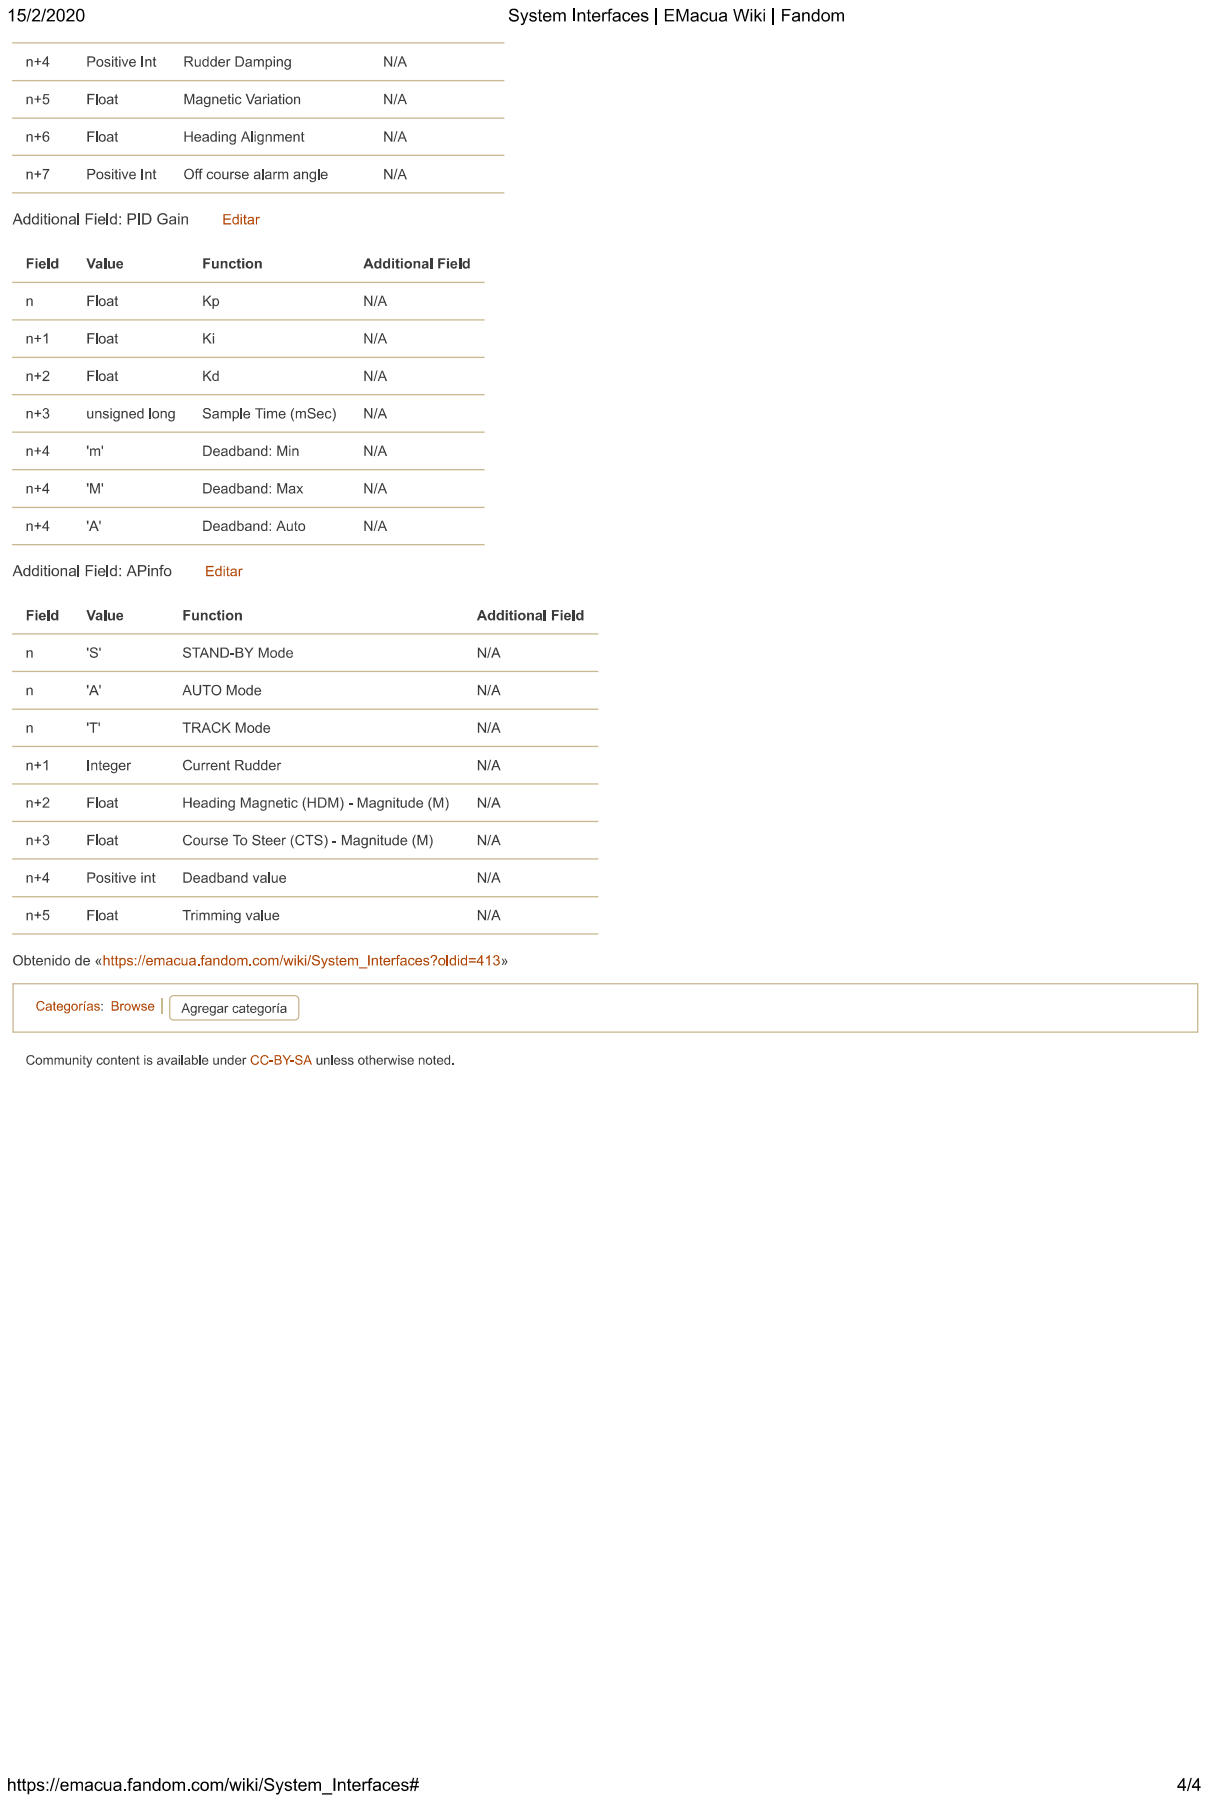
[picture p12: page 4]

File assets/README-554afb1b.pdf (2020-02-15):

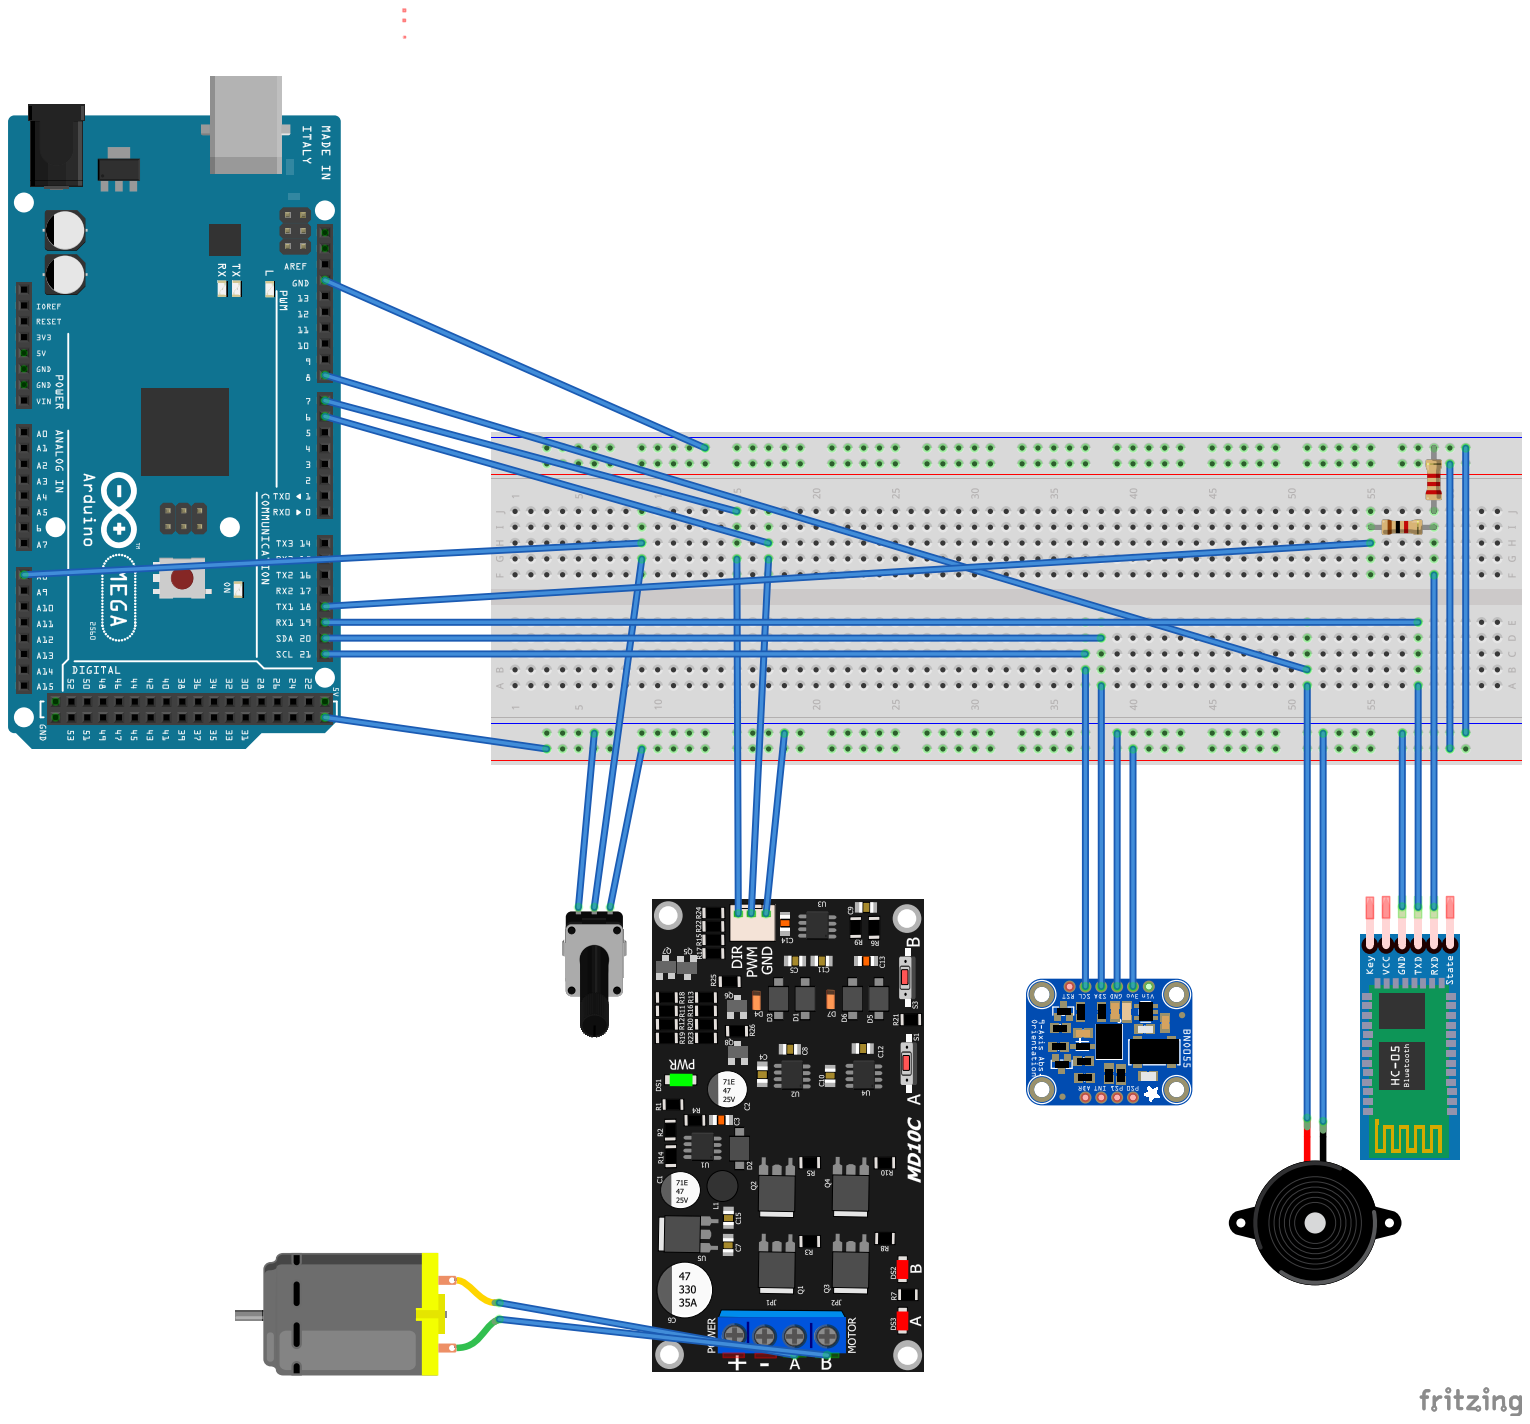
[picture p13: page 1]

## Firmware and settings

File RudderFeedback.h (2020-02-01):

/*
 * RudderFeedback.h
 *
 *  Created on: 16 abr. 2017
 *      Author: Sergio
 */

#ifndef RUDDERFEEDBACK_H_
#define RUDDERFEEDBACK_H_

#include <Arduino.h>
#include "GPSport.h" // Serial NMEA IF Configuration in GPSPort.h not in Fenix.ino!

//#define VIRTUAL_ACTUATOR // SPM TODO: Comment when actuator is connected

//#define PIN_RUDDER A15
//#define PIN_RUDDER_NAME "A15"

#define PIN_RUDDER A8
#define PIN_RUDDER_NAME "A8"

// FEEDBACK PARAMETERS HARDCODED
// Parameters for linear actuator THAT DEPENDS ON THE SPECIFIC LINEAR ACTUATOR

// MIN/MAX VALUES FOR IDEAL LINEAR ACTUATOR
#define D_MIN_FEEDBACK 0 //AS READ FROM PIN_RUDDER IN THE RETRACTED POSITION OF THE ACTUATOR
#define D_MAX_FEEDBACK 1023 //AS READ FROM PIN_RUDDER IN THE EXTENDED POSITION OF THE ACTUATOR

// VALUES FOR THE SLOW LINEAR ACTUATOR
//#define MIN_FEEDBACK 268 //AS READ FROM PIN_RUDDER IN THE RETRACTED POSITION OF THE ACTUATOR
//#define MAX_FEEDBACK 754 //AS READ FROM PIN_RUDDER IN THE EXTENDED POSITION OF THE ACTUATOR
#define DEFAULT_ERROR_FEEDBACK 10 //A number between 0 and 1023 to protect linear actuator from overuse
//#define STROKE 300 //actuator stroke in mm

// ADDITIONAL RUDDER PARAMETERS
// Parameters for rudder
#define DEFAULT_MRA 512 // MRA = ABS_MIN_RUDDER Value in degrees *10
#define RUDDER_LENGHT 1023 // Value in degrees *10
//Rudder status
enum e_rudderStatus {EXTENDED, CENTERED, RETRACTED};
enum e_feedback_status {FEEDBACK_OK, OK_VIRTUAL, ERROR_TOO_BIG};

class RudderFeedback {
public:
	RudderFeedback(int MRA = DEFAULT_MRA, int error = DEFAULT_ERROR_FEEDBACK, int deltaCenterOfRudder=0, int minFeedback=D_MIN_FEEDBACK, int maxFeedback=D_MAX_FEEDBACK);
	virtual ~RudderFeedback();

	int getErrorFeedback () const {
		return _errorFeedback;
	}

	int getCurrentRudder() const {
		return (_currentRudder  - _center_of_rudder);
	}

	int changeRudder(int delta_rudder);

	e_rudderStatus getRudderStatus() const;

	int getFeedback() const;

	int getDeltaCenterOfRudder() const {
		return _delta_center_of_rudder;
	}


	int getCenterOfRudder() const {
		return _center_of_rudder;
	}

	int getMinRudder() const {
		return (-_MRA);
	}

	int getMaxRudder() const {
		return (_MRA-1);
	}

	int getLimitMaxFeedback() const {
		return _limit_max_feedback;
	}

	int getLimitMinFeedback() const {
		return _limit_min_feedback;
	}


	// FEEDBACK CALIBRATION FUNCTIONS
	void start_calFeedback();
	void set_calFeedback();

	void setLimitMinFeedback(
			int limitMinFeedback = D_MIN_FEEDBACK) {
		_limit_min_feedback = limitMinFeedback + 2* getErrorFeedback ();
	}

	void setLimitMaxFeedback(
			int limitMaxFeedback = D_MAX_FEEDBACK) {
		_limit_max_feedback = limitMaxFeedback - 2* getErrorFeedback ();
	}

protected:
	//fn to change independent variables in Standby mode
	void setDeltaCenterOfRudder(int deltaCenterOfRudder = 0, bool recalc = true);
	void setErrorFeedback (int error_feedback = DEFAULT_ERROR_FEEDBACK, bool recalc = true);
	int getMaxFeedback() const {
		return _max_feedback;
	}
	int getMinFeedback() const {
		return _min_feedback;
	}
	void setMinFeedback (int min_feedback = 0, bool recalc = true);
	void setMaxFeedback (int max_feedback = D_MAX_FEEDBACK, bool recalc = true);
	void setMRA (int MRA = DEFAULT_MRA, bool recalc = true);
	e_feedback_status setup(bool b_ibit=false); // b_ibit=true->performs IBIT at the end
	e_feedback_status IBIT();
	int updateCurrentRudder();
	int toRudder(int feedback) {
		return feedback*_ratio;
	};
	int toFeeback(int rudder) {
		return rudder/_ratio;
	}

	void compute_Cal_Feedback();


private:
	//independent variables
	int _errorFeedback = DEFAULT_ERROR_FEEDBACK;
	int _min_feedback = D_MIN_FEEDBACK;//A number between 0 and 1023.
	int _max_feedback = D_MAX_FEEDBACK;//A number between 0 and 1023.
	int _delta_center_of_rudder =0;
	int _MRA = DEFAULT_MRA; // MIN_RUDDER = -MRA; MAX_RUDDER = MRA-1

	//dependent variables
	int _limit_min_feedback = (D_MIN_FEEDBACK+DEFAULT_ERROR_FEEDBACK);//A number between 0 and 1023.
	int _limit_max_feedback = (D_MAX_FEEDBACK-DEFAULT_ERROR_FEEDBACK);//A number between 0 and 1023.
	int _feedback_lenght = (D_MAX_FEEDBACK-D_MIN_FEEDBACK-(2*DEFAULT_ERROR_FEEDBACK)); //(LIMIT_MAX_FEEDBACK-(LIMIT_MIN_FEEDBACK));
	float _ratio = RUDDER_LENGHT/_feedback_lenght;
	int _center_of_rudder;
	int _currentRudder;//Actuator feedback in rudder scale

	//Values to calibrate linear actuator
	int _cal_minFeedback=D_MAX_FEEDBACK;
	int _cal_maxFeedback=D_MIN_FEEDBACK;
	int _cal_restore_error = DEFAULT_ERROR_FEEDBACK;

	// IBIT functions
	char* get_PIN_RUDDER() {return (PIN_RUDDER_NAME);}
	int rudder_IBIT ();


};

#endif /* RUDDERFEEDBACK_H_ */

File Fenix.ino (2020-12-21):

//header TODO

#include <Arduino.h>

// Comment any IF not implemented. Activating an IF without HW device installed will cause unexpected effects
//#define HMI_LCDKEYPAD // LCDKeypad IF
#include "GPSport.h" // Serial NMEA,Debug and Bluetooth IF Configuration in GPSPort.h not in Fenix.ino!

#ifdef HMI_BT

#include "BT.h"
#endif

#ifdef HMI_LCDKEYPAD
#include "LCDKeyPad.h"
#endif

#ifdef SERIAL_IF_AVAILABLE
#include "IF_NMEA.h"

#ifndef NMEAGPS_INTERRUPT_PROCESSING
	  #error You must define NMEAGPS_INTERRUPT_PROCESSING in NMEAGPS_cfg.h!
#endif

#endif

#include "MacuaAutopilot.h"

// INSTANTIATE OBJECTS
Macua_Autopilot MyPilot;

#ifdef HMI_LCDKEYPAD
LCDKeyPad MyLCDKP(&MyPilot);
#endif

#ifdef HMI_BT
BT MyBT(&MyPilot);
#endif

#ifdef SERIAL_IF_AVAILABLE
static IF_NMEA parserNMEA(&MyPilot); // This parses received characters

static void NMEAisr( uint8_t c )
{
  parserNMEA.handle( c );

} // GPSisr
#endif

void setup()
{
	// Setup NMEA IF if defined
#ifdef SERIAL_IF_AVAILABLE
	parserNMEA.setup();

	gpsPort.attachInterrupt( NMEAisr );
	gpsPort.begin( 9600 );
#endif

	// Setup LCDKeypad if defined
	#ifdef HMI_LCDKEYPAD
	MyLCDKP.setup();
	#endif

	// Setup Bluetooth if defined
	#ifdef HMI_BT
	MyBT.setup();
	// SPM INI VIRTUINOCM
	MyBT.begin(MyBT.onReceived,MyBT.onRequested,256);  //Start Virtuino. Set the buffer to 256. With this buffer Virtuino can control about 28 pins (1 command = 9bytes) The T(text) commands with 20 characters need 20+6 bytes
	  //virtuino.key="1234";                       //This is the Virtuino password. Only requests the start with this key are accepted from the library
	// SPM INI VIRTUINOCM
	#endif

	// Setup autopilot
	switch (MyPilot.setup()){
		case SETUP_OK:
			DEBUG_print("Start\n");
			break;
		case IMU_ERROR:
		case FEEDBACK_ERROR:
			MyPilot.buzzer_Error();
			DEBUG_print("Stop\n");
			while(1){;}
			break;
	}


#ifdef SERIAL_IF_AVAILABLE
    //Start transmission of NMEA messages
    parserNMEA.startTX();
#endif

}

void loop()
{
	// Refresh NMEA IF if defined
	#ifdef SERIAL_IF_AVAILABLE
	parserNMEA.refresh();
	#endif

	// Refresh LCDKeypad if defined
	#ifdef HMI_LCDKEYPAD
	MyLCDKP.refresh();
	#endif

	// Refresh Bluetooth if defined
	#ifdef HMI_BT

	//delay(500);
	MyBT.refresh();
	#endif

	// New pilot iteration
	if (MyPilot.Compute() == RUNNING_ERROR) {

		//DEBUG_PORT.println( F("PILOT ERROR") );

		// pilot error. Turn light on and beep
		#ifdef HMI_LCDKEYPAD
		MyLCDKP.turnLight(ON);
		//MyLCDKP.print("PILOT: Error");
		#endif

		//TODO: beep
		}

}

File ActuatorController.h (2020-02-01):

/*
 * ActuatorManager.h
 *
 *  Created on: 16 abr. 2017
 *      Author: Sergio
 */

#ifndef ACTUATORCONTROLLER_H_
#define ACTUATORCONTROLLER_H_

#include <Arduino.h>
#include "GPSport.h" // Serial NMEA IF Configuration in GPSPort.h not in Fenix.ino!

#define PIN_PWM 6
#define PIN_DIR 7

#define MIN_SPEED 0
#define MAX_SPEED 255

// setup status
enum e_dir {EXTEND, RETRACT};

// ACTUATOR PARAMETERS
// PROTECT LINEAR ACTUATOR FROM HIGH THROUGHPUT DUE TO CHANGE OF DIRECTION
   #define DELAY_DIRCHANGE 500 //delay after change of dir in ms

class ActuatorController {
public:
	ActuatorController();
	virtual ~ActuatorController();

	int setSpeed (int);
	e_dir setDir (e_dir);

	e_dir getDir() const {
		return _currentDirection;
	}

	int getSpeed() const {
		return _currentSpeed;
	}
	int get_PIN_PWM() {return PIN_PWM;}
	int get_PIN_DIR() {return PIN_DIR;}


protected:
	void setup();

	//Feedback Calibration
	void cal_FBK_move(e_dir dir);

private:
	e_dir _currentDirection= EXTEND; // EXTEND or RETRACT
	int _currentSpeed=0; //Value speed between 0 and 255
	//bool blocked_dirCharge = false;
	//const unsigned long delay_dirChange;

	void IBIT();
};

#endif /* ACTUATORCONTROLLER_H_ */

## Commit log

2020-02-15 Closure of Fenix V0.1
    [Fenix.fzz]
2020-02-21 Various changes not impacting code
    [Fenix.fzz]
2020-02-22 Added media for schematics
2020-02-28 Improved IMU Low message
